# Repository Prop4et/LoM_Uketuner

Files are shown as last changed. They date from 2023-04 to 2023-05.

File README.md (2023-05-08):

# Automatic Uke Tuner
The project consists in creating a (semi) automatic uke tuner by using an arduino uno board, a microphone and a stepper motor. Everything is also connected to a small circuit used to see which note we are currently tuning, if we are in tune and used also to rotate the stepper motor and put it in the correct position

### The idea
The idea was to create a somehow portable automatic uke tuner which uses a stepper motor to turn the uke keys in relation to the frequencies listened through a microphone. Everything needed to be controlled by an Arduino UNO R3, based on the atmega328P chip.

### The execution
During the development of the project different ideas actually overlapped and were explored, starting from a portable tuner the project evolved into a non portable tuner with the Arduino controlling 4 different stepper motors, one for each uke key. This way i can create a place where i could put the uke and tune it automatically. This idea was crushed when the first stepper that i tried wasn't strong enough to turn the keys and so i needed to find a stronger stepper that meant find a more expensive motor. Moreover the stepper needed the H-Bridge to be controlled, starting with a L298N bridge that could be used to power and controll a stepper and to alsow power the arduino and then shifting towards the drv8825 driver which allowed for a more precise control of the stepper but couldn't split the voltage spullied to the motor thus the need to a separate power source for the Arduino.

The final and probably tallest wall to face was the design of the key-crankshaft connector. I had an initial idea in mind for the connector with 3 cylinders put on the verices of a triangle to hold the key in position. This shape wasn't holding the key correcly so i changed it to 4 cylinders staying on the vertices of a rectangle. 
What needed to change was also the coupler between the crankshaft and the actual holder for the key. With the first motor i had a circular shaped crankshaft and i had to design a coupler that could be tightened with some screws. These motors didn't have enough power so by going to the strongest one i had another shape for the crankshaft that allowed me to change the shape of the coupler making it in one piece. The crankshaft has in fact a flat section that helps in holdin the coupler in place.

## Components used
+ Arduino UNO R3
+ Stepper NEMA 17HE19-2004S
+ Driver drv8825
+ Power source ~16V
+ Capacitor 100uF
+ Microphone Diamex Ky-037
+ LCD screen
+ I2C adapter for LCD
+ 2 LEDs (one green, one red)
+ 2 resistors (160 ohm)
+ 2 buttons  
+ 10K Ohm potentiometer
+ 1 switch
+ jumpers and wires

## Pinout
| Arduino | Diamex Ky-037 |
| --- | --- |
| GND | VCC |
| GND | GND |
| A0 | A0 |
| D6 | D0 |

| Arduino | LCD |
| --- | --- |
| 5V | VCC |
| GND | GND |
| A4 | SDA |
| A5 | SCL |

| Arduino | DRV 8825 |
| --- | --- |
| 5V | M0 |
| 5V | RST |
| 5V | SLP |
| 12 | dir |
| 11 | stp |
| GND | GND Logic |

| DRV 8825 | NEMA17/Power Source |
| --- | --- |
| VMOT | 16V |
| GNDMOT | GND |
| B2 | B+ |
| B1 | B- |
| A1 | A+ |
| A2 | A- |

| Arduino | Red LED |
| --- | --- |
| 5 | VCC |
| GND | GND |

| Arduino | Green LED |
| --- | --- |
| 4 | VCC |
| GND | GND |

| Arduino | Selector Button |
| --- | --- |
| 5V | VCC |
| 3 | GND |

| Arduino | Motor Button |
| --- | --- |
| 5V | VCC |
| 2 | GND |

| Arduino | Potentiometer |
| --- | --- |
| 5V | VCC |
| A1 | SDA | 
| GND | GND |

## 3D designs



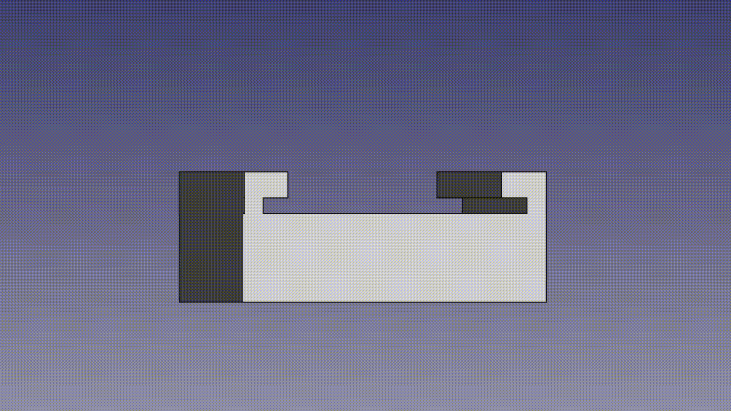
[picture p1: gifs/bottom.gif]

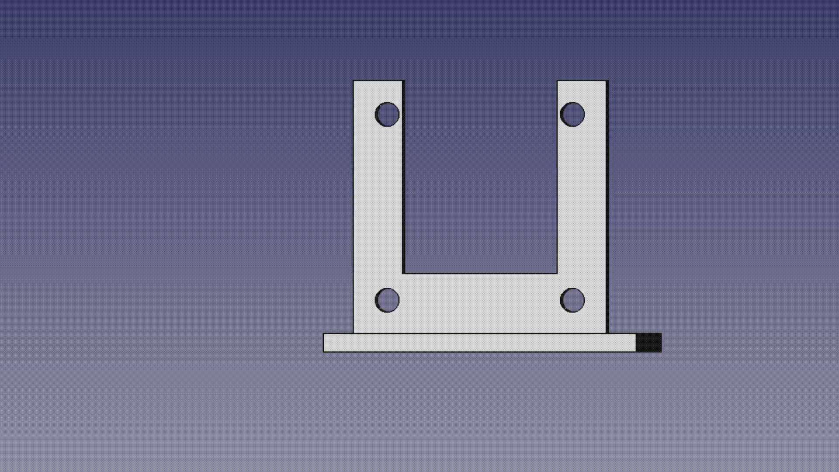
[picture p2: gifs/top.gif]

Every 3D model is [here](https://github.com/Prop4et/LoM_Uketuner/tree/master/3D)
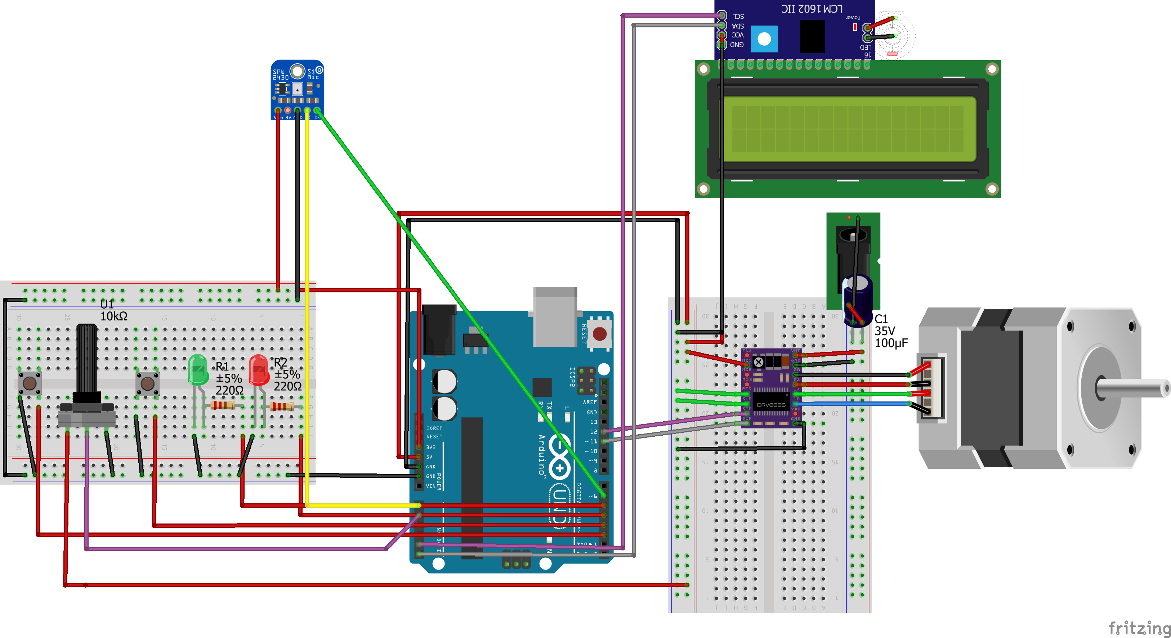
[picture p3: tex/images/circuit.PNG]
circuit

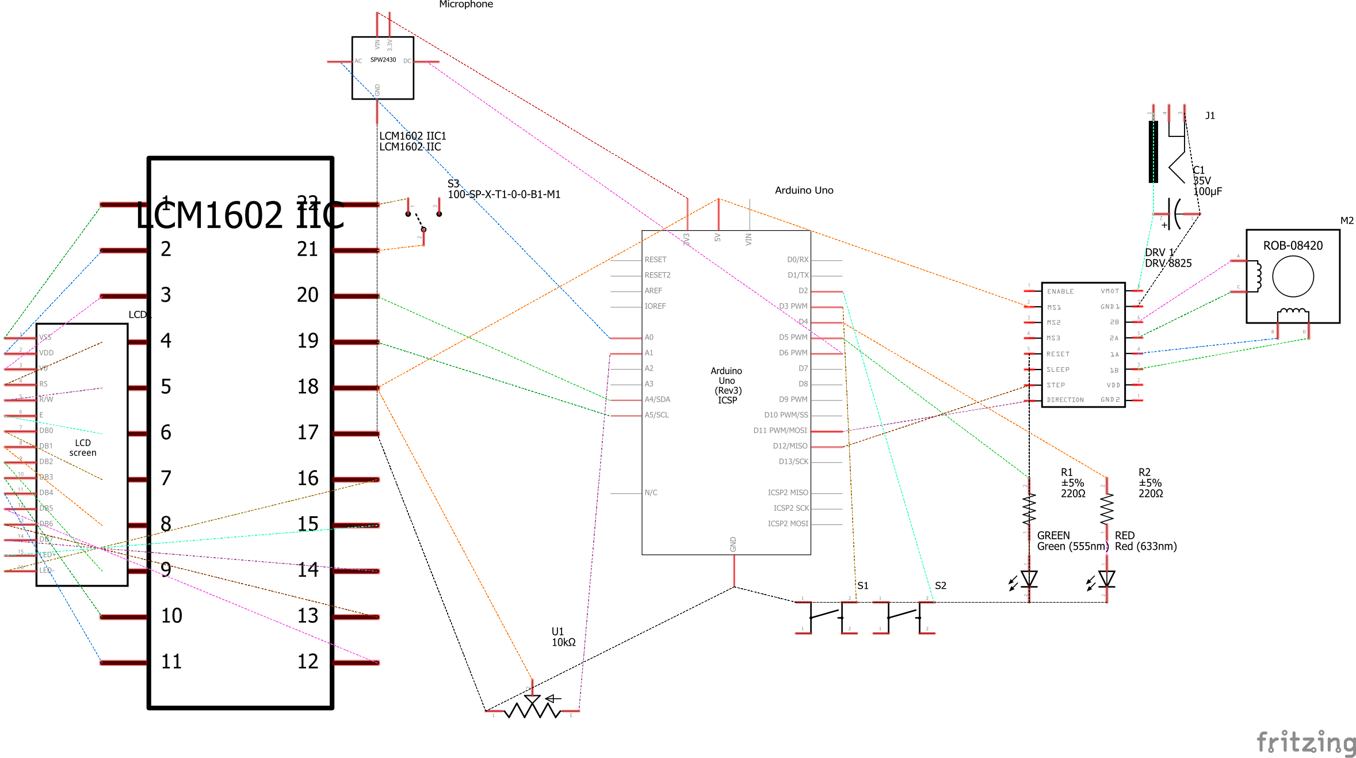
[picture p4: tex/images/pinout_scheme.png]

final
For more information you can check the [PDF](tex/main.pdf), the video of the tuning process can be found [here](https://youtu.be/HMqDMtXxrdM). The quality is not the highest but i cannot help the outside noises, eventhough that demonstrates that the microphone senstivity helps.

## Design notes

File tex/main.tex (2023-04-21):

\documentclass[a4paper,12pt]{article}
% Package to make citations superscrit with brackets
\usepackage[super,square]{natbib}
% Package to change margin size
\usepackage{anysize}
\marginsize{2cm}{2cm}{1cm}{2cm}
% Package to make headers
\usepackage{fancyhdr}
\renewcommand{\headrulewidth}{0pt}
% Package for highligths
\usepackage{soul}
% Colors for the references links
\usepackage[dvipsnames]{xcolor}
% Package to link references
\usepackage{hyperref}
\usepackage{animate}
\usepackage{graphicx}
\usepackage{float}
\hypersetup{
    colorlinks=true,
    linkcolor=black,
    citecolor=CadetBlue,
    filecolor=CadetBlue,      
    urlcolor=CadetBlue,
}
% Package for lorem ipsum
\usepackage{lipsum}
% Package for multicolumn
\usepackage{multicol}
\setlength\columnsep{18pt}
% Sets bastract
\renewenvironment{abstract}
 {\par\noindent\textbf{\abstractname} \ignorespaces:}
 {\par\noindent\medskip}

\begin{document}
\begin{center}
\Large{\textbf{Uke Tuner}}
\vspace{0.4cm}
\normalsize
\\ \textbf{Francesco Biancucci;} 984303 \\
\vspace{0.1cm}

\small{\textit{Laboratory of Making} 20/04/2023}
\medskip
\normalsize
\end{center}
{\color{gray}\hrule}
\vspace{0.4cm}
\begin{abstract}
\input{./abstract.tex}
\end{abstract}
{\color{gray}\hrule}
\medskip
\begin{multicols}{2}
\tableofcontents
\section{Introduction}
The project consists in a system designed to tune a ukulele without the user actively having to turn the keys. The initial idea was to create a somehow portable automatic uke tuner which uses a stepper motor to turn the uke keys in relation to the frequencies listened through a microphone. Everything needed to be controlled by an Arduino UNO R3, based on the Atmega328P chip. During the development of the project the idea shifted from a portable tuner to some sort of fixed station with four motors that needed only the uke to be put in it and then would tune the played string.\\
The final idea that was a compromise between the two because of two main reasons:
\begin{itemize}
    \item costs; using four motors makes the work easier and the project would look prettier, but the trade off between costs and the actual usefulness wasn't worth it.
    \item size; using a stepper motor such the one of choice doesn't actually save space, so the solution cannot be considered portable. Also the motor needs a decent amount of power to run, so the power supply adds to that.
\end{itemize}
\section{Hardware Design}
When talking about the system design we should consider two different components. The circuit part, with the selection of the different components that create the final design, and the software developed to actually control the hardware.
\subsection{Circuit}
The design of the circuit went through different iterations and changed in the time, following the changes that were made because of the knowledge acquired during the development process or the necessities that needed to be satisfied to make the system work.\\
The first version of the system used a L298N H-bridge, in Fig. \ref{fig:l298n}.
\begin{figure}[H]
        \begin{center}
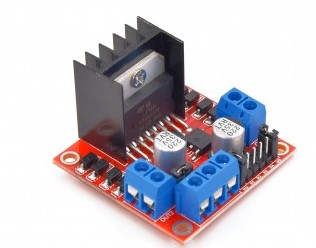
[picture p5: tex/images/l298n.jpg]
            
            \caption{L298N}
            \label{fig:l298n}
        \end{center}
    \end{figure}
The L298N is a high voltage, high current dual full-bridge driver made of two integrated H-bridge inside that can support up to 46V and 2A per bridge. While with the L298N was possible to extract the source for powering the Arduino, it wasn't possible to control the output current that can go up to 2A. Such flow of current, if not handled, could damage the attached stepper motor. Moreover the dimensions of the L298N don't make it a versatile component that can be used in a circuit that doesn't take a lot of space.\\
For these reasons I decided to change from the L298N to the DRV8825 driver which allows for current flow control.
\begin{figure}[H]
    \begin{center}
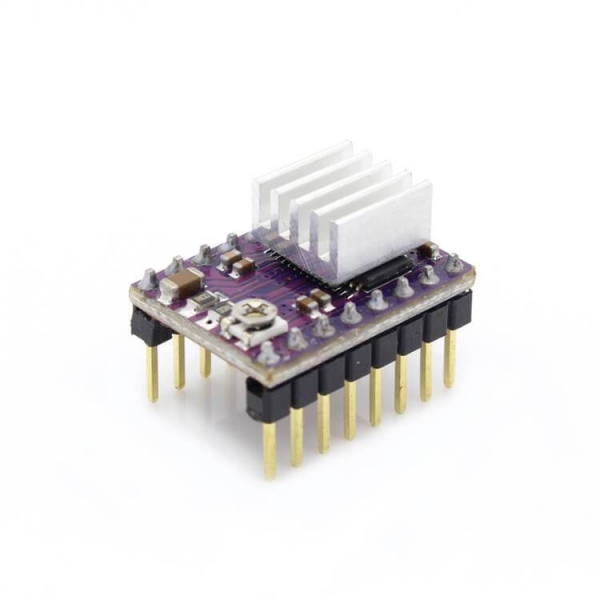
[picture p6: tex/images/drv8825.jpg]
        
        \caption{DRV8825}
        \label{fig:drv8825}
    \end{center}
\end{figure}
\begin{figure}[H]
    \begin{center}
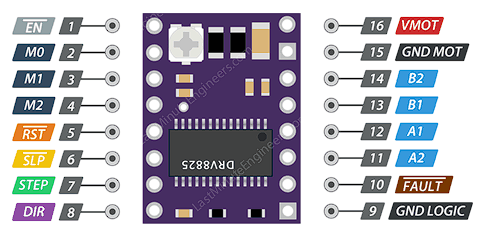
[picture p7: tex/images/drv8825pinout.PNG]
        
        \caption{DRV8825 pinout}
        \label{fig:drv8825_pinout}
    \end{center}
\end{figure}
On a first glance it may seem an overkill but it has other useful functions that were then used inside the project. The first difference with the L298N, as said, is the ability to control the output current through an integrated resistor. The current limit is in fact determined by measuring the voltage at the ref pin (that is the resistor screw); the \textit{Vref} value should be half of the nominal current limit of the stepper.\\
By using Fig. \ref{fig:drv8825_pinout} I'll now explain the different meaning of the pins and what are the other functionalities offered by this driver.
\begin{itemize}
    \item EN is the enable pin and it is pulled LOW by default. When pulled LOW the driver is enabled, so by default the driver is enabled and can be used for a shutdown mechanism.
    \item MO, M1 and M2 are the pins used to define the step size resolution. By setting these pins to LOW/HIGH in combination is possible to control how much the stepper turns. By default these three pins are all pulled low meaning, as shown in Table \ref{tab:steps}, that the resolution is by defaul at full step. The final configuration of the driver actually used the half step to allow for better precision when turning the key.
    \item SLP is an active low pin that puts the driver to sleep when pulled LOW. It wasn't used since the tuner needs to be working almost all the time when it is powered on.
    \item RST is an active low pin too. When pulled Low the steps are ignored and it resets the driver.
    \item STEP is the controller of the microstpes of the motor. For each time it receives an HIGH pulse it drives the motor following the resolution of the microstep. E.g. if the stepper has a step of 1.8° and the resolution is full step then the motor rotates of 1.8°.
    \item DIR is the input pin that controls the direction of the motor. When pulled HIGH it turns the motor clockwise, counterclockwise when pulled LOW.
    \item VMOT e GNDMOT supply power to the motor. These pins can support a voltage between 8.2V and 45V. The module is not completely protected against voltage spikes, so as an additional protection a 100$\mu$F capacitor is put between the power supply and the pins.
    \item GND LOGIC is the ground for the logic level of the driver. It doesn't have an input logic pin since it has an internal 3V3 voltage regulator that allows the driver to drain from the motor power supply, but it needs the ground to be connected to the logic element.
    \item B2, B1, A1, A2 are the pins controlling the coils of the steppers.
    \item FAULT is a pin that when driven LOW disables the entire chip until reset or VMOT is removed. It is usually shorted to SLP.
\end{itemize}
The DRV8825 also comes with a small heatsink that helps in dissipating the heat.\\
The other elements that were changed during the development phase were the stepper itself, and I'll talk about it later, and the microphone. The first microphone used was suitable to detect audio but it wasn't able to detect the different frequencies, having only a digital output (i had this microphone already from another project). Then I switched to a microphone able to output a analog signal that could be interpreted. The problem this time around was that every sound was picked up so I ended going for the KY-037 microphone that has a reasonable precision on the analog readings and it also has a potentiometer on board that allows to adjust the threshold sensitivity.\\
\begin{figure}[H]
    \begin{center}
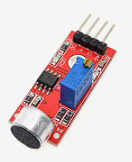
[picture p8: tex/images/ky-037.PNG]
        
        \caption{ky-037}
        \label{fig:ky-037}
    \end{center}
\end{figure}
The other bits of circuitry used were two LEDs, one red and one green, used to signal if the uke string was in tune (green blink) or not (red blink). These two LEDs are connected on the 5V output line. Both LEDs have their own voltage drop and their rated current limit, from which the value of the resistances are computed. By using the Ohm's law \[V=R*I\] it is possible to get the resistances for the two LEDs.
\begin{itemize}
    \item Red led: 1.8V drop and 20mA rated current $\rightarrow$ R = (5-1.8)/0.02 = 160Ohm
    \item Green led: 2.0V drop and 20mA rated current $\rightarrow$ R = (5-2)/0.02 = 150Ohm
\end{itemize}
So i used two 200Ohm resistances.\\
The circuit also includes a LCD screen with a IIC adapter. The LCD is used to display some information during the tuning process, such as the selected string to tune or the played note when tuning. The LCD pins were soldered to the IIC adapter that allows for a smooth communication with the MCU and it also has a potentiometer on board that is used to regulate the back light of the LCD.
\begin{figure}[H]
    \begin{center}
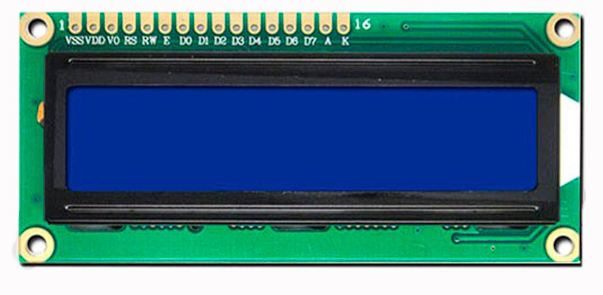
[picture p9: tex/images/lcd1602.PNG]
        
        \caption{LCD}
        \label{fig:LCD}
    \end{center}
\end{figure}
To complete the circuit there is a switch that is used turn the LCD back light on and off.\\
It is reasonable to call the set of LCD and LEDs the control block of the tuner, since it is the part that allows to check the state of the tuning process. On this control block there are two more buttons and a potentiometer.\\
The first button is used to select the string to tune. After some considerations and after having studied other system used to tune guitars/ukuleles it was clear that the automatic process of recognizing the string that needs to be tuned is something that is based only on the "nearest string to the played tune" way of recognizing the string. For example if i played the G string, but the frequencies played were nearer to the A frequencies the tuner would default to tune to A. Since the system uses a motor to tune the string it was considered safer to select the string manually to avoid snapping the strings in case of a bad recognition happening.\\
The other button is used to manually turn the stepper to position the connector between the stepper and the uke key in a way that allows for connection. The potentiometer in this case is used to control the rotational speed of the motor.
\subsection{Stepper Motors}
The first used stepper motor in the project is the NEMA 17HS10-0704S that is a bipolar stepper motor with a step resolution of 1.8° and a rated current of 0.7A (Fig. \ref{fig:NEMA17HS10}. Following what has been said above the \textit{Vref} was set to 0.35A.
\begin{figure}[H]
    \begin{center}
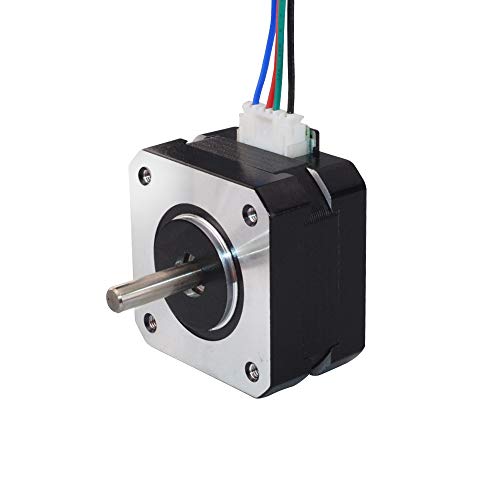
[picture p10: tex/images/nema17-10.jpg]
        
        \caption{NEMA17-10}
        \label{fig:NEMA17-10}
    \end{center}
\end{figure}
As shown in the above figure the stepper has a cylindrical crankshaft that needs to be somehow connected to the uke key. There are couplers for this kind of crankshaft that can be bought but i also needed a way to connect the other end of the coupler to the key, so i decided to design my own coupler and my own connector. In Fig. \ref{fig:coupler} the coupler design si shown; to have a more accurate view it is possible to check the \href{https://github.com/Prop4et/LoM_Uketuner/blob/master/3D/coupler_part.stl}{stl file} loaded on github. The coupler has four sockets for the screws and for the nuts that are used to tighten it to the crankshaft. Since I designed the coupler I decided to create a little slot on the top of the crankshaft section that would help in keeping in place the fork used to lock the uke key (Fig. \ref{fig:grab}).
\begin{figure}[H]
    \centering
    \animategraphics[autoplay, loop, width=6cm]{24}{images/coupler/goupler-}{0}{167}
    \caption{Coupler}
    \label{fig:coupler}
\end{figure}
\begin{figure}[H]
    \centering
    \animategraphics[autoplay, loop, width=6cm]{24}{images/grab/grab-}{0}{82}
    \caption{Fork}
    \label{fig:grab}
\end{figure}
This design had some problems and needed to go different tries before being used. The first problem was that the measures used to design all the sockets were too precise and didn't take into account the tolerances that a 3D printer has. After a couple of iterations I managed to obtain a product that was usable, but during the test phase with the motor it showed two major issues:
\begin{itemize}
    \item The shape of the fork wasn't able to hold the key in place correctly, letting the key sliding laterally and then out of the fork
    \item The motor wasn't strong enought to turn the keys (I had adjusted the fork with a string on the outside that helped in keeping the key in place momentarily)
\end{itemize}
To solve the insufficient torque of the stepper I checked the pull out torque of the NEMA 17HS10 in Fig \ref{fig:NEMA17HS10torque} and then i tried the stepper with the settings at which the torque should be at its maximum point but it still didn't manage to turn the keys. So i changed the stepper and I went for a NEMA 17HS19 (in figure \ref{fig:nema17-19}) that has more torque and it also manages to keep almost the same amount of torque for a wider range of round per minutes (Fig. \ref{fig:NEMA17HS19torque}). This gives more room to work with and more room for error.
\begin{figure}[H]
    \begin{center}
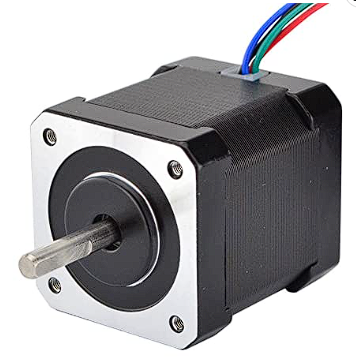
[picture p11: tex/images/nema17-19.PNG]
        
        \caption{NEMA17-19}
        \label{fig:nema17-19}
    \end{center}
\end{figure}
The NEMA 17HS19 has a different crankshaft design too. There is a slice on the cylinder that made me rethink the design of the coupler not only on the fork side.
\begin{figure}[H]
    \centering
    \animategraphics[autoplay, loop, width=6cm]{24}{images/grabnew/grabnew-}{0}{97}
    \caption{Final coupler design}
    \label{fig:grabnew}
\end{figure}
For a better view of the new coupler design it could be helpful to check the \href{https://github.com/Prop4et/LoM_Uketuner/blob/master/3D/grabnew.stl}{.stl file}, but the main characteristics of this new coupler are:
\begin{itemize}
    \item built all in one piece, allowing for more precision since there is no tolerance in the movement of the fork with respect to the crankshaft 
    \item no screws needed, the small slice in the crankshaft allows for locking without needing to tighten the coupler, if the hole is of the right size
    \item the fork has four cylinders in a rectangular shape to lock the keys instead of three
\end{itemize}
Ideally this coupler works perfectly, but there are cases that even with the sliced section it slips, so i thought about adding two screholes on a side and removing a bit of material from a section of the cylinder, leaving an open space that will close up when tightening the screws. I don't know about the bending characteristics of the PLA though, so i opted for not trying that solution.\\
Another problem that showed with the coupler finally working is that che cylinders aren't fused strongly enouhg on the circular plate, so the strength needed to turn the keys sometimes caused a cylinder to snap.\\
The other two designed pieces create a system to keep the stepper in place and to align it to the keys of the uke. In fact the two forward keys are at a lower height than the back ones. So i created a holder (Fig. \ref{fig:holder}) for the stepper and a platform \ref{fig:platform} in wich the holder would slot in to make up for this height difference.
\begin{figure}[H]
    \centering
    \animategraphics[autoplay, loop, width=6cm]{24}{images/top/top-}{0}{91}
    \caption{Stepper holder}
    \label{fig:holder}
\end{figure}\begin{figure}[H]
    \centering
    \animategraphics[autoplay, loop, width=6cm]{24}{images/bottom/bottom-}{0}{185}
    \caption{Platform}
    \label{fig:platform}
\end{figure}
The final pinout for the circuit is at \ref{fig:pinout}
\section{Software Design}
Everthing in the tuner is handled by an Arduino UNO R3. This board was chosen because it is easy to program, it has a lot of different libraries and i actually had the board already. There are some limitations in using the Arduino UNO R3 for this project, such as the memory used to collect the frequency samples or the time that an analogRead takes on the Arduino UNO R3.\\
The software for the tuner is made of three main different parts that interacts between them, the LCD, the microphone and the stepper.\\
\subsection{LCD}
The LCD is handled through the \textit{LiquidCrystal\_I2C} library that allows for easy read and writes through the LCD I2C bus. By default the LCD address is 0x27 and this value is passed as a parameter for the initialization of the LCD object, together with the number of columns and the number of rows. The library is based on the Wire.h library for the IIC communication and by default this library uses the A4 pin for the data line and the A5 for the clock line (on the Arduino UNO).\\
The only self implemented function was the scroll function. The default one in fact would scroll until the end of the line and then will fill the screen with blank spaces until the first character of the sequence and start it again. I didn't like this effect and i wanted the sentece to restart right after the last letter, so i made my own function. On the LCD the currently selected string to tune is shown and it also shows the most recently played note. The scroll doesn't stop during the blinking of the led, but it stops during the period in which the stepper turns. The call to write to the I2C was to slow and stopped the rotation of the stepper so instead of stopping the stepper i decided to stop the writing process.

\subsection(Stepper)
The stepper motor is controlled only through two pins from the Arduino. Initially I tested the stepper with the raw code that sent a pulse to the STP pin every 2000$\mu$s to see if it worked. Then i went ahead and used the AccelStepper library that allowed to control the acceleration of the stepper and also to set a limit speed. That way i was able to check if the stepper was able to turn the keys at max torque since i had the value for the speed. Also the half step pin was connected on the driver to allow for both more precision and more torque.\\
The thing I didn't like about the AccelStepper library is the smooth acceleration that is given to reach the speed, so i reverted back to the raw code and tested which was a reasonable interval of pulses to make the stepper turn the uke keys. To do so i added the button and the potentiometer that allowed me to change the interval in real time, as a function of the resistance read by the potentiometer. This mechanism then stayed in the circuit and it is used to align the coupler fork to the uke key when the string that needs tuning is changed.

\subsection{Microphone}
The microphone was probably the most difficult thing to handle by the software, and the piece where the Arduino limitations showed up more.\\
Firstly the digital pin value is read at every loop to see if a sound is detected. If that's the case then the analog input is read and that is passed to the ArduinoFFT library. The arduinoFFT library is the library that helps in generating a Fourier transofmration of the signal, the fast derives from the mathematical method used that helps in reducing the complexity of the classic method to compute the Fourier transofmration. \\
First of all a sampling interval should be defined; to have a decent sampling the sampling frequency should be two times the highest frequency that needs to be sampled. The highest note on a string on the uke is at 440Hz, and the uke string seems to be almost snapping at 630Hz. The Arduino UNO has a clock frequency of 8MHz (16Mhz if using the crystal oscillator), so it should handle a sampling with a frequency of 2048Hz.
\[sampling\_period[\mu s] =\]
\[=round(1000000 * (1.0 / SF));\]
The second factor that influences the sampling is the amount of samples that could possibly be taken. The Arduino UNO doens't have a lot of memory, so it is possible to get maximum 128 samples.\\
The samples are then passed to the ArduinoFFT library, the real part of the values is used for the windowing function and then it is computed while the imaginary data must be put at 0 during the sampling step to avoid wrong calculations and overflows. Finally the major peak is extracted, giving the frequency of the note played.\\
This mechanism works pretty well but every note played has its own tolerance, and this tolerance has been measured by comparing the actual frequency of the string played when in tune (measure with another tuned) and the frequency returned by the ArduinoFFT library. After this process the \textit{tolerances} array was created. Another problem that the ArduinoFFT library has is that it isn't able to precisly recognize the lower (below B3) notes; instead of recognizing the right note it goes an octave higher and recognizes it as A4 or something in that range. So in case the C4 string is lower the code cheats and brings the string to a more understandable tune.

In the end the stepper spins following a simple formula. If the difference between the played tune and the desired tune is higher than 2 then it spins for at least a complete revolution. Otherwise it checks if the difference in frequency is high enough. If it is it spins for half a revolution, otherwise it spins for a number of step proportional to the frequency difference multiplied for a random factor between 10 and 15.\\
This random factor was determined after observing that with a factor of 15 the tuning process would usually get to the right tune pretty fast, but it could get stuck on some frequency since the key was always turned of the same amount, only changing the direction. The randomness helps in resolving this issuse.
\section{Conclusions}
In conclusion I would say that through this project I learned a lot more about stepper motors and interestengly enough the thing that I learned to do the most is design 3D parts, for which i used FreeCAD, that can then be printed. I don't own a 3D printer and I have never designed something in 3D before, so picking up this skill was interesting. Every 3D printed model is available \href{https://github.com/Prop4et/LoM_Uketuner/tree/master/3D}{here}\\
At the end of the project a box to contain all the circuitry was designed but it wasn't possible to print it since the high amount of time it needed and I don't own a 3D printer, the design is however present in Fig. \ref{fig:topbox} and in Fig. \ref{fig:botbox}. I decided to solder the circuit anyway, because it made me think it could give a sense of precision but without touching the Arduino (it could come in handy for other projects). The final result, without the box, isn't the most attractive one \ref{fig:final}.
\subsection{Final considerations}
There is room for improvements under every aspect. The possibility to create a box to contain everything, the idea of putting 4 different steppers with a clever design to hold the motor in place, the implementation of automatic recognition of the string that needs to be tuned and also the optimal utilization of the DRV8825 driver by using the SLP pin to put it to sleep and other little improvements.
\end{multicols}
\newpage
\section{Appendix}
\begin{figure}[H]
    \begin{center}
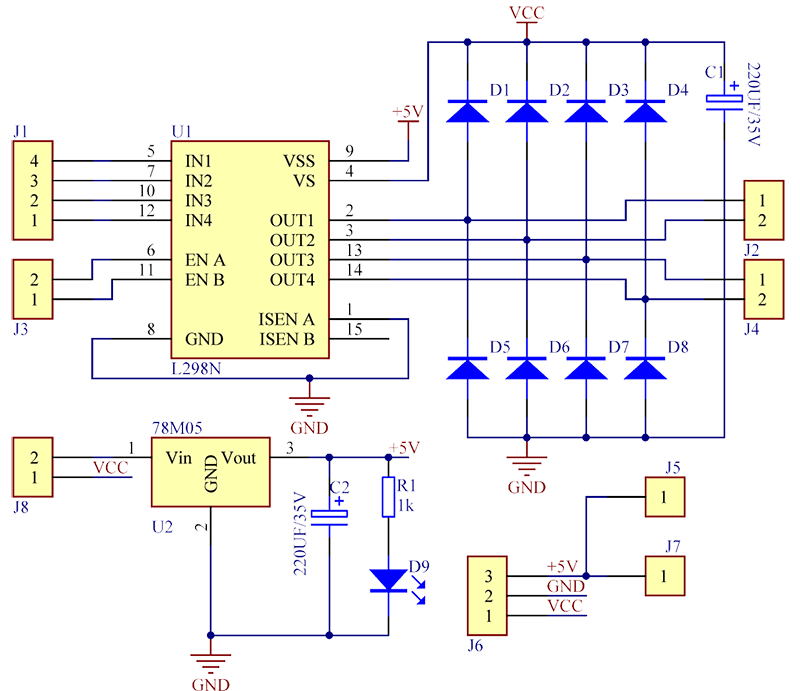
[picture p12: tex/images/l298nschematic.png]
        
        \caption{L298N Schematic}
        \label{fig:l298nschematic}
    \end{center}
\end{figure}

\begin{table}[H]
\centering
\begin{tabular}{ | p{2cm}  p{2cm}  p{2cm} p{3cm}| } 
\hline
\textbf{M0} & \textbf{M1} & \textbf{M2} & \textbf{Resolution} \\
\hline
\hline
Low & Low & Low & Full Step\\
High & Low & Low & Half Step\\
Low & High & Low & 1/4 Step\\
High & High & Low & 1/8 Step\\
Low & Low & High & 1/16 Step\\
High & Low & High & 1/32 Step\\
Low & High & High & 1/32 Step\\
High & High & High & 1/32 Step\\
 \hline
\end{tabular}
\caption{Steps Resolution}
 \label{tab:steps}
 \end{table}
 \begin{figure}[H]
    \begin{center}
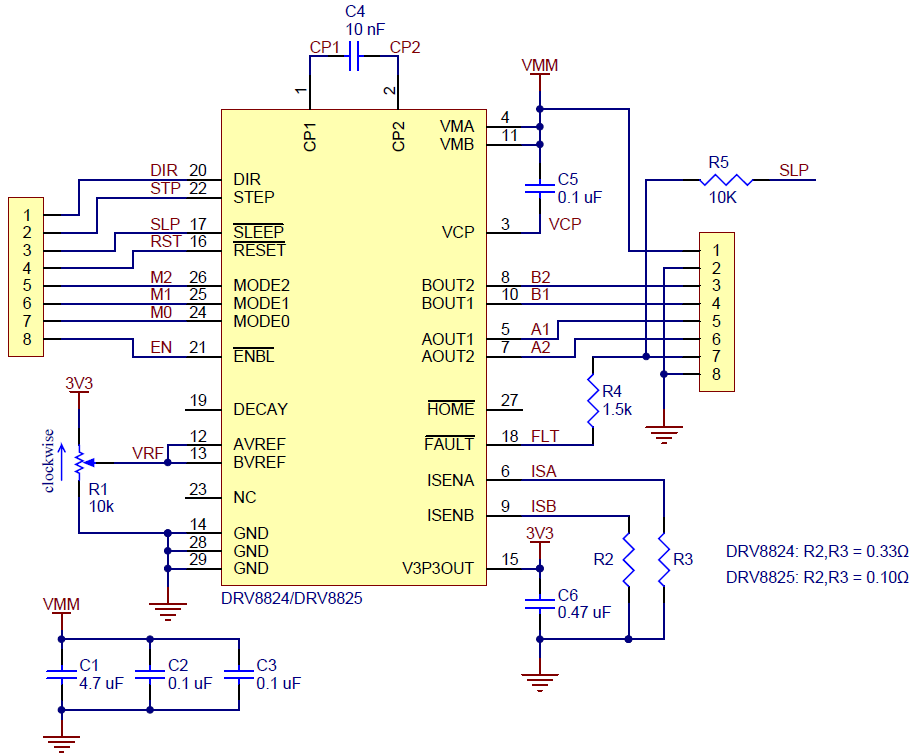
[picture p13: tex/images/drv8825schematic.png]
        
        \caption{DRV8825 Schematic}
        \label{fig:drv8825schematic}
    \end{center}
\end{figure}
 \begin{figure}[H]
    \begin{center}
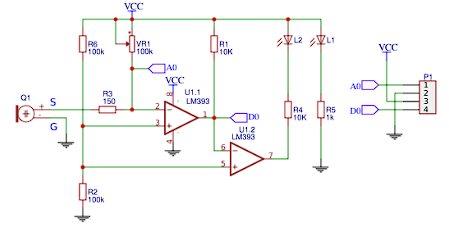
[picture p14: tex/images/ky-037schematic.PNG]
        
        \caption{ky-037 Schematic}
        \label{fig:ky-037schematic}
    \end{center}
\end{figure}
 \begin{figure}[H]
    \begin{center}
        
        \caption{NEMA17HS10 from \href{http://www.omc-stepperonline.com}{Stepperonline}}
        \label{fig:NEMA17HS10}
    \end{center}
\end{figure}
\begin{figure}[H]
    \begin{center}
        
        \caption{NEMA17HS19 from \href{http://www.omc-stepperonline.com}{Stepperonline}}
        \label{fig:NEMA17HS19}
    \end{center}
\end{figure}
\begin{figure}[H]
    \begin{center}
        
        \caption{NEMA17HS10 Torque Curve from \href{http://www.omc-stepperonline.com}{Stepperonline}}
        \label{fig:NEMA17HS10torque}
    \end{center}
\end{figure}
\begin{figure}[H]
    \begin{center}
        
        \caption{NEMA17HS19 Torque Curve from \href{http://www.omc-stepperonline.com}{Stepperonline}}
        \label{fig:NEMA17HS19torque}
    \end{center}
\end{figure}
\begin{figure}[H]
    \begin{center}
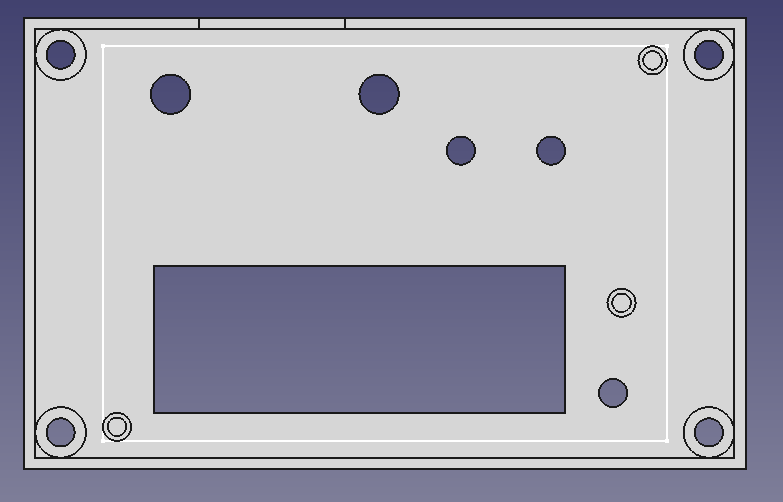
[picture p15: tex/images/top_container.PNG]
        
        \caption{Top section of the Box}
        \label{fig:topbox}
    \end{center}
\end{figure}
\begin{figure}[H]
    \begin{center}
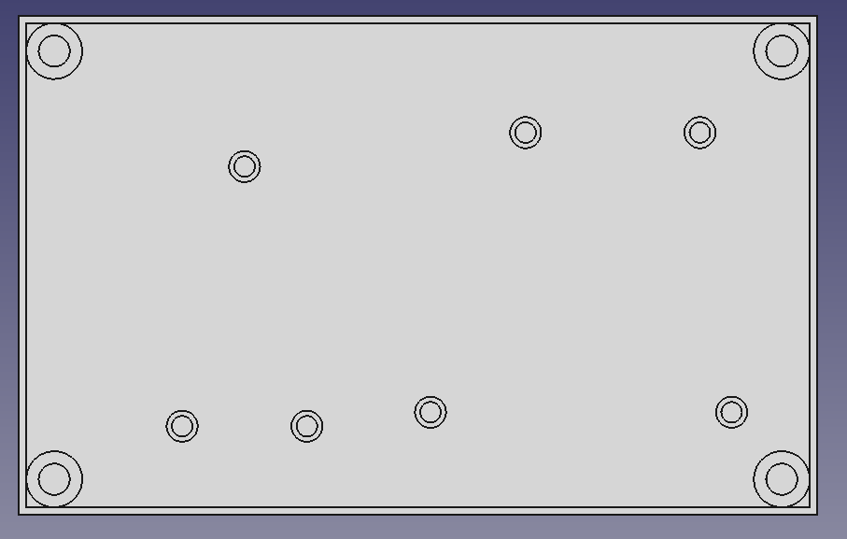
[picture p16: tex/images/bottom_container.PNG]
        
        \caption{Bottom section of the Box}
        \label{fig:botbox}
    \end{center}
\end{figure}
\begin{figure}[H]
    \begin{center}
        
        \caption{Circuit pinout}
        \label{fig:pinout}
    \end{center}
\end{figure}

\begin{figure}[H]
    \begin{center}
        
        \caption{Final product}
        \label{fig:final}
    \end{center}
\end{figure}

\end{document}

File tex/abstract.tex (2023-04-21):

The goal of the project was to design, program and build an automatic ukulele tuner which should be able to recognize the played note and then tune the selected string accordingly. The project was made of two main parts that needed to be designed and developed. The hardware, consisting of the circuit and the physical elements that made the motor interact with the uke and the software controlling the hardware.

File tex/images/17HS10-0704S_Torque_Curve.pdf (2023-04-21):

## 17HS10-0704S PULL OUT TORQUE(0.7A/P 24V HALF STEP)

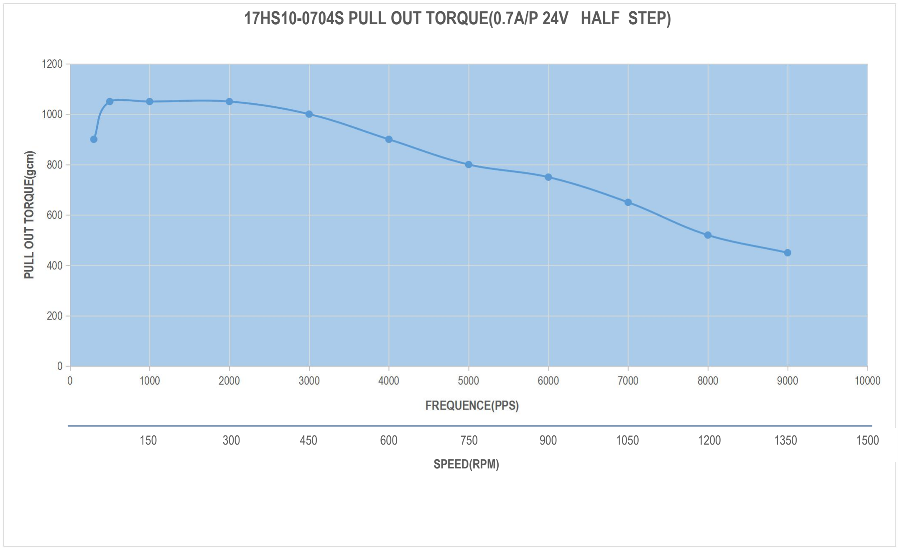
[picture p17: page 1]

150 | 300 | 450 | 600 | 750 | 900 | 1050 | 1200 | 1350 | 1500
| | | | SPEED(RPM)

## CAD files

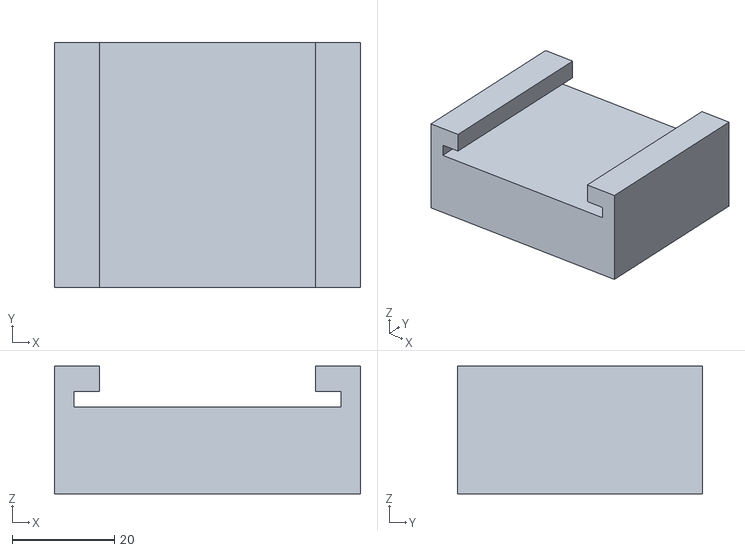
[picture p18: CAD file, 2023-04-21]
3D/bot.stl
60.0 x 48.0 x 25.0

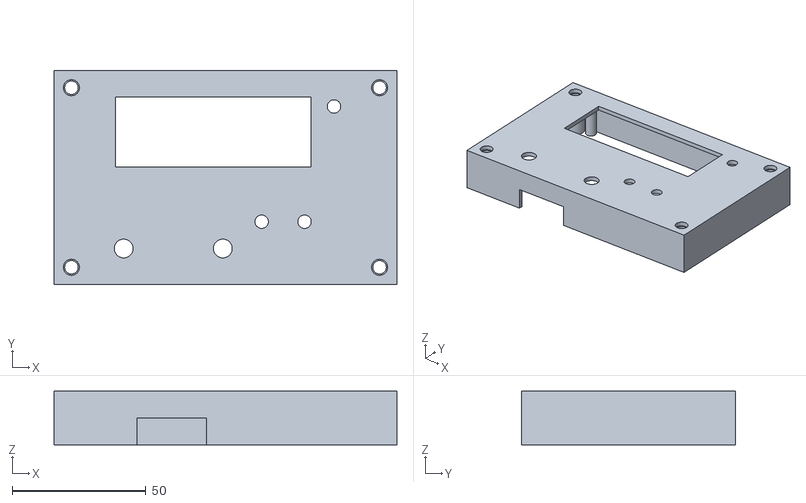
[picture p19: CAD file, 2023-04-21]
3D/top_container.stl
128.0 x 80.0 x 20.0

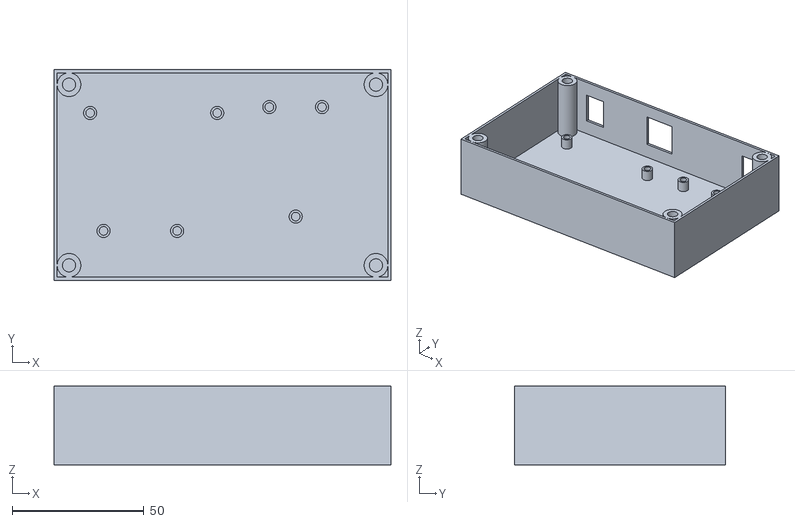
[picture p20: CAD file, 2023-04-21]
3D/bottom_container.stl
128.0 x 80.0 x 30.0

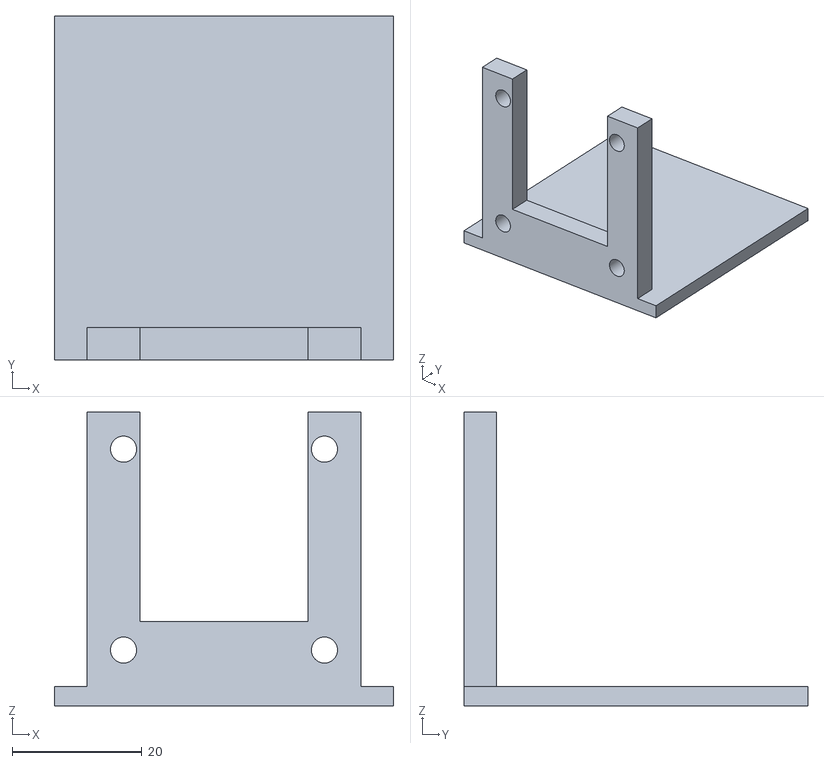
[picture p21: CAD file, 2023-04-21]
3D/top.stl
52.3 x 53.0 x 45.3

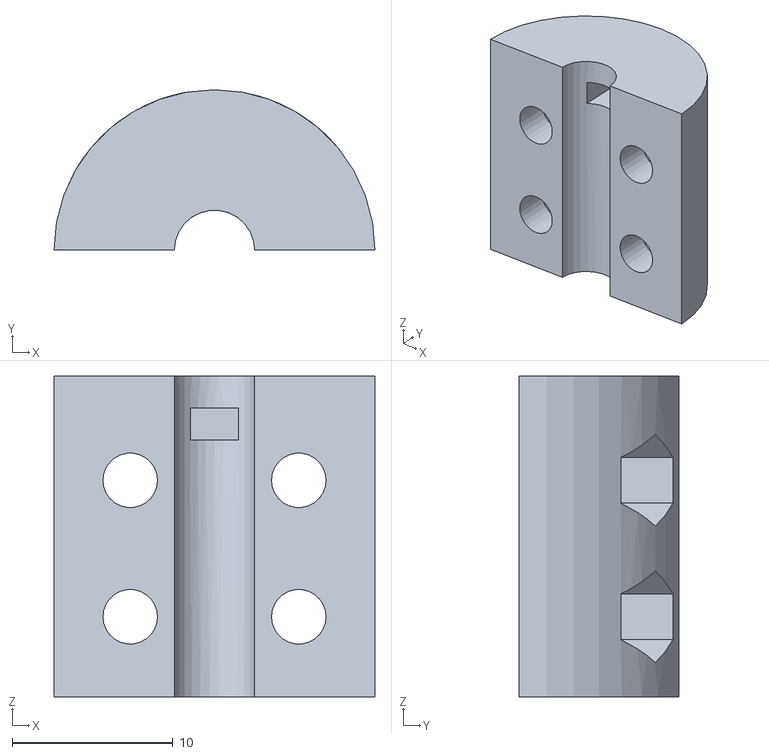
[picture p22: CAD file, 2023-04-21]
3D/coupler_part.stl
20.0 x 10.00 x 20.0

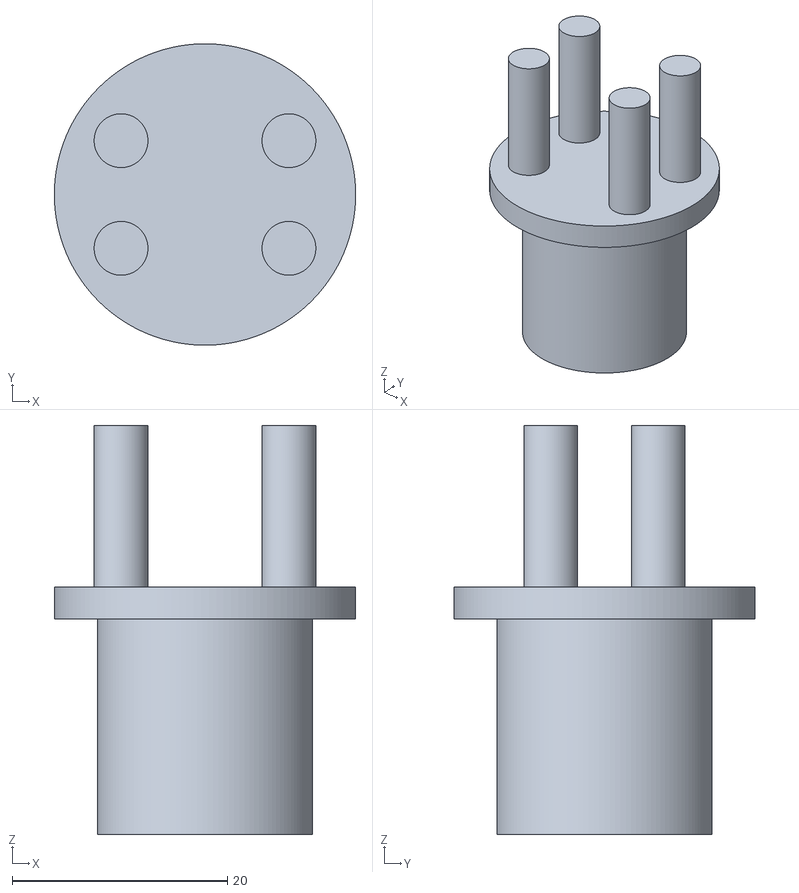
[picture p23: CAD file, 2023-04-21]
3D/grabnew.stl
28.0 x 28.0 x 38.0

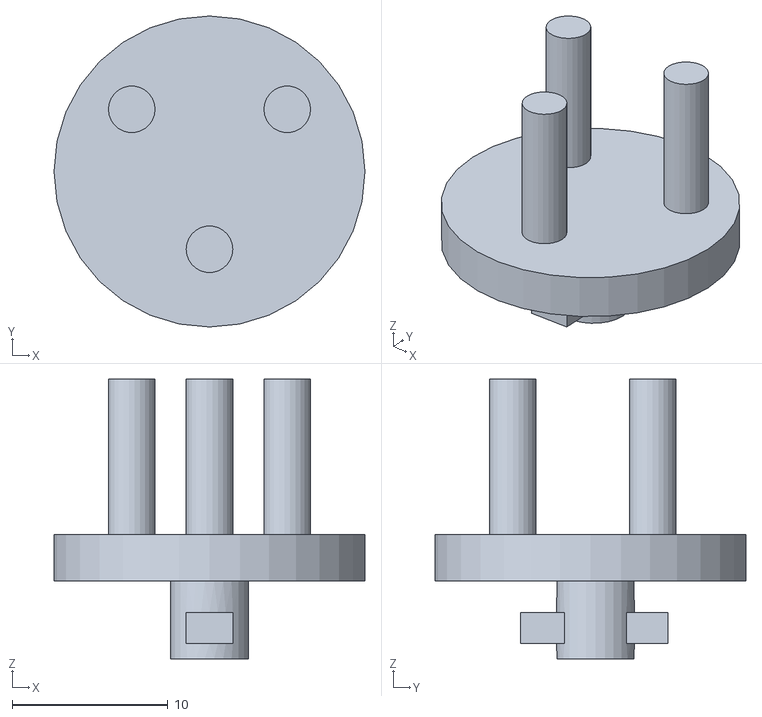
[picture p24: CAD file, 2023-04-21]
3D/grabold.stl
20.0 x 20.0 x 18.0

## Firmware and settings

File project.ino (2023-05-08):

#include "arduinoFFT.h"
#include <LiquidCrystal_I2C.h>
//#include <AccelStepper.h>

#define SAMPLES 128 //max amount of samples for arduino uno
#define SAMPLING_FREQUENCY 2048 //must be 2*highest expected frequency, A is 440Hz and after 630Hz seems like it's about to snap
#define SCREENLEN 17
#define FULLSTEPS 400
#define MAXFREQ 500.00
#define MINFREQ 225.00

#define PRINTTOLERANCE 10

#define NTUNEALL 14
#define NTUNE 4

#define analogPin A0//read the analog input -> frequency
#define digitalPin 6//read the digital input -> activation
#define redLedPin 5//red led pin 
#define greenLedPin 4//green led pin

#define btnPin 3 //switch pin
#define rotatePin 2//pin to rotate the motor
#define potenPin A1 //potentiometer reading pin
 //complete circle at half step

#define stepPin 12;
#define dirPin 11;
int delayRotation = 0;
//AccelStepper myStepper(motorInterfaceType, stepPin, dirPin);

//save variables for the notes (cannot loop unfortunately) from B3 to A4#

const float printTolerances[NTUNEALL] = {2, 2, 3.3, 5, 4, 4, 6, 6, 5.5, 8, 6, 8.5, 7, 6};
const float tunesFreq[NTUNEALL] = {233.08, 246.94, 261.63, 277.18, 293.66, 311.13, 329.63, 349.23, 369.99, 392.00, 415.30, 440.00, 466.16, 493.88};
const char* tunesAll[NTUNEALL] = {"A3", "B3", "C4", "C4#", "D4", "D4#", "E4", "F4", "F4#", "G4", "G4#", "A4", "A4#", "B4"};


unsigned int samplingPeriod;
unsigned long microSeconds;

//G C E A


char dest[30];
const char* tunes[NTUNE] = {"G4", "C4", "E4", "A4"};
const float freqs[NTUNE] = {392.00, 261.63, 329.63, 440.00};
const float tolerances[NTUNE] = {8, 5.3, 6, 10.0};
const float ranges[NTUNE] = {1.5, 0.8, 0.6, 1.2};

int currBtnState;
int prevBtnState;
int rotateBtnState;
int prevRotateBtnState;
int currTune = -1;

//bool tuning = false;
bool buttonPressedFirst = false; //0 never pressed, 1 pressed 1 time, 2 do nothing
bool freqOOB = false;
const int sampleWindow = 50; // Sample window width in mS (50 mS = 20Hz)
unsigned int sample;

unsigned long scrollTime = 0;
//LCD_I2C lcd(0x27);
LiquidCrystal_I2C lcd(0x27, 16, 2);
char beginSentence[] = "Press the button to start ";
int sentenceCounter = 0;
void setup() {
  //Setup LCD
  Serial.begin(115200);
  lcd.init();
  lcd.backlight();
  lcd.clear();
  lcd.setCursor(0, 0);
  lcd.print(beginSentence);

  //setup mic pin
  pinMode(analogPin, INPUT);
  pinMode(digitalPin, INPUT);

  //setup led pins
  pinMode(redLedPin, OUTPUT);
  pinMode(greenLedPin, OUTPUT);
  digitalWrite(redLedPin, LOW);
  digitalWrite(greenLedPin, LOW);
  
  //setup button pin
  pinMode(btnPin, INPUT_PULLUP);
  currBtnState = digitalRead(btnPin);
  prevBtnState = currBtnState;

  pinMode(rotatePin, INPUT_PULLUP);
  rotateBtnState = digitalRead(rotatePin);
  prevRotateBtnState = rotatePin;
  
  
  //setup fastfft parameters
  samplingPeriod = round(1000000 * (1.0 / SAMPLING_FREQUENCY));
  
  //setup motor parameters
  scrollTime = millis();
}


int scrollFun2(char* sentence, int len){
  lcd.setCursor(0,0);
  lcd.print("                       ");
  delayMicroseconds(2000);
  lcd.setCursor(0,0);
  int i = sentenceCounter;
  int j = 0;
  while(j < SCREENLEN){
    lcd.print(sentence[i]);
    i += 1;
    i = i % len;
    lcd.setCursor(j, 0);
    j++;
  }
  sentenceCounter += 1;
  sentenceCounter %= len;
}


void blink(int led) {
  digitalWrite(led, HIGH);
  unsigned long curr = millis();
  while(millis() - curr < 2000){
    if(millis() - scrollTime>= 500){
      scrollFun2(dest, strlen(dest));
      scrollTime = millis();
    }
  }
  digitalWrite(led, LOW);
}
void spin(int dir, int stepDiff, float freqDiff){
  
  int stepCounter = 0;
  digitalWrite(dirPin, dir);
  if(stepDiff >= 2){
    int appSteps = FULLSTEPS*(int(stepDiff/2));
    
    while(stepCounter < appSteps){
      digitalWrite(stepPin, HIGH);
      delayMicroseconds(1000);
      digitalWrite(stepPin, LOW);
      delayMicroseconds(1000);
      //cannot put print in here cause it's heavy
      stepCounter += 1;
    }
  }
  else{
    int steps;
    if(freqDiff > 17)
      steps = 200;
    else
      steps = random(10,15)*freqDiff;
    
    
    while(stepCounter < steps){
      digitalWrite(stepPin, HIGH);
      delayMicroseconds(1000);
      digitalWrite(stepPin, LOW);
      delayMicroseconds(1000);
      //cannot put print in here cause it's heavy
      stepCounter += 1;
    }
  }
  stepCounter = 0;
}

int speedUp() {

  int customDelay = analogRead(potenPin); // Reads the potentiometer
  int newCustom = map(customDelay, 0, 1023, 500, 2000); // Convrests the read values of the potentiometer from 0 to 1023 into desireded delay values (300 to 4000)
  return newCustom;  

}

void rotateMotor(){
  rotateBtnState = digitalRead(rotatePin);
  if (rotateBtnState != prevRotateBtnState) {
    digitalWrite(dirPin, 1);
    while(!rotateBtnState){
      int appRotation = speedUp();
      if(abs(delayRotation - appRotation) > 150){
        delayRotation = appRotation;
      }
      digitalWrite(stepPin, HIGH);
      delayMicroseconds(delayRotation);
      digitalWrite(stepPin, LOW);
      delayMicroseconds(delayRotation);
      rotateBtnState = digitalRead(rotatePin); 
    }
    prevRotateBtnState = rotateBtnState;    
  }
}

void switchNote() {
  currBtnState = digitalRead(btnPin);
  if (currBtnState != prevBtnState) {
    if (!currBtnState) {
      buttonPressedFirst = true;
      lcd.clear();
      sentenceCounter = 0;
      currTune += 1;
      currTune %= NTUNE;
      strncpy(dest, "Selected: ", 12);
      strncat(dest, tunes[currTune], strlen(tunes[currTune]));
      strcat(dest, "(");
      int fint = (int)freqs[currTune];
      char app[3] = {" "};
      sprintf(app, "%d", fint);
      strncat(dest, app, 3);
      strcat(dest, ".00)  ");
      lcd.print(dest);
      for (int i = 0; i < 3; i++) {
        lcd.setCursor(i, 1); //deleting the # in case it exists
        lcd.print(" ");
      }
    }
    prevBtnState = currBtnState;
    delayMicroseconds(200);
  }
}



void loop () {
  switchNote();
  rotateMotor();
  if(!buttonPressedFirst){
    if(millis() - scrollTime>= 500){
      scrollFun2(beginSentence, strlen(beginSentence));
      scrollTime = millis();
    }
    return;
  }
  
  if(millis() - scrollTime>= 500){
    scrollFun2(dest, strlen(dest));
    scrollTime = millis();
  }
  //redeclared everytime for memory
  double vReal[SAMPLES]; //array of real samples
  double vImg[SAMPLES]; //array of img samples
  int val = digitalRead(digitalPin);

  if (val == HIGH) {
    for (int i = 0; i < SAMPLES; i++) {
      microSeconds = micros();

      vReal[i] = analogRead(analogPin);
      vImg[i] = 0;

      while (micros() < (microSeconds + samplingPeriod)) {
        //do nothing
      }
    }

    freqOOB = false;
    //process to FFT the samples
    arduinoFFT FFT = arduinoFFT(vReal, vImg, SAMPLES, SAMPLING_FREQUENCY);
    FFT.Windowing(FFT_WIN_TYP_HAMMING, FFT_FORWARD);
    FFT.Compute(FFT_FORWARD);
    FFT.ComplexToMagnitude();

    //find the "main" frequency
    double freq = FFT.MajorPeak();
    Serial.println(freq);
    //working on the frequency
    //frequency out of bounds
    if ( freq < MINFREQ || freq > MAXFREQ ){
      if(!freqOOB){
        lcd.setCursor(0, 1); //moving the cursor back to the beginning and printing
        lcd.print("Frequency OOB");
        freqOOB = true;
      }
    }
    
    //select played frequency to print
    int i = 0;
    if(!freqOOB){
      while (i < NTUNEALL-1 && !(freq >= tunesFreq[i] + printTolerances[i] - PRINTTOLERANCE && freq < tunesFreq[i+1]))
        i += 1;
      freq - tunesFreq[i] < tunesFreq[i+1] - freq ? i : i+=1;
      freqOOB = false;
      //print on lcd
      lcd.setCursor(0, 1); //deleting the # in case it exists
      lcd.print("              ");
      delayMicroseconds(2000);
      lcd.setCursor(0, 1); //moving the cursor back to the beginning and printing
      
      lcd.print(tunesAll[i]);
      //if played tune is the same as the selected one
    }
    if (!freqOOB && (freqs[currTune] + tolerances[currTune] - ranges[currTune] <= freq) && (freqs[currTune] + tolerances[currTune] + ranges[currTune] >= freq) && i != NTUNEALL){
      blink(greenLedPin);  
    }
    else if(!freqOOB) {
      float freqDiff = abs(freq - (freqs[currTune]+tolerances[currTune]));
      int dir = 0; 
      blink(redLedPin);
      if(currTune == 1 && freq > 360){
         spin(1, 4, 0);
         return;
      }
      //tuning = true;
      int stepDiff = 0;
      int findex = i;
      if (freqs[currTune]+ tolerances[currTune] < freq) { //selected is less than played
        dir = 0;
        while(findex >= 0 && tunesFreq[findex] > freqs[currTune]){
          
          stepDiff+=1;
          findex-=1;
        }
      }
      if (freqs[currTune] + tolerances[currTune]/1.5 > freq) { //selected is higher than played 

        dir = 1;

        while(findex < NTUNEALL && tunesFreq[findex] < freqs[currTune]){
          
          stepDiff+=1;
          findex+=1;
          
        }
      }
      spin(dir, stepDiff, freqDiff);
      
      
    }
  }

}

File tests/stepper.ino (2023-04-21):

// Include the AccelStepper Library
#include <AccelStepper.h>

// Define pin connections
const int dirPin = 13;
const int stepPin = 12;

// Define motor interface type
#define motorInterfaceType 1

// Creates an instance
AccelStepper myStepper(motorInterfaceType, stepPin, dirPin);

void setup() {
  // set the maximum speed, acceleration factor,
  // initial speed and the target position
  myStepper.setMaxSpeed(600);
  myStepper.setAcceleration(150);
  myStepper.setSpeed(300);
  myStepper.moveTo(10000);
}

void loop() {
  // Change direction once the motor reaches target position
  // Move the motor one step
  myStepper.run();
}

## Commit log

2023-05-08 added electric scheme
    [pinout.fzz]
2023-05-08 edit scheme
    [pinout.fzz]
